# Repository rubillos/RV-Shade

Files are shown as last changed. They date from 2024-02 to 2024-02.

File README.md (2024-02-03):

# RV-Shade: HomeKit RV Shade controller

1. [Features](#features)
2. [Background](#background)
3. [Hardware](#hardware)
4. [Schematic](#schematic)
5. [Board Layout](#board-layout)
6. [Wiring](#wiring)
7. [Firmware Setup](#firmware)
8. [3D Printing](#3dprint)

## Features

* Arduino based circuit which intercepts the signals from the dash switch on an RV front shade to give HomeKit control.
* Built with an Adafruit QT Py ESP32-S3.
* Fits inside the front dash.
* STL files for a 3D printed case are included.

## Background

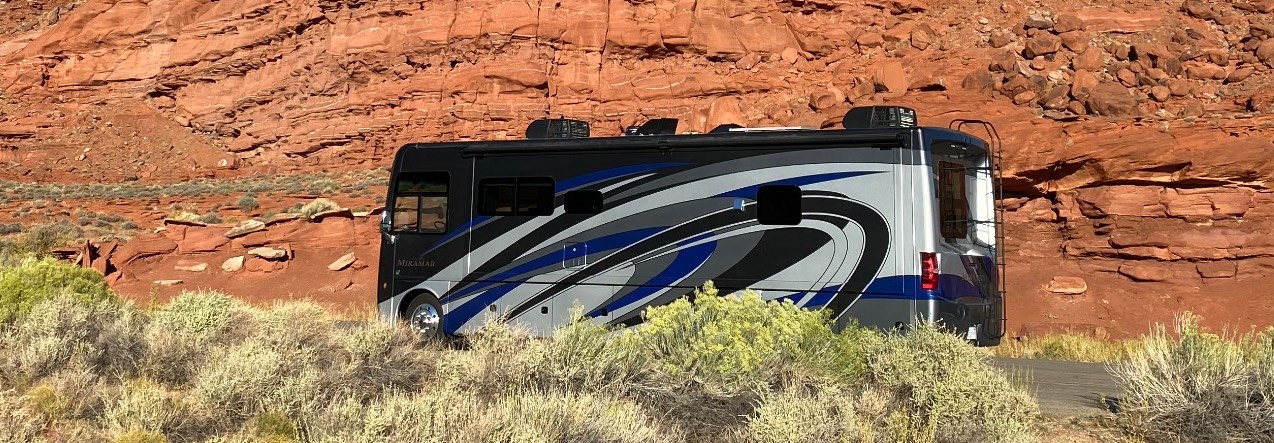
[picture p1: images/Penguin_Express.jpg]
Penguin Express


After purchasing a class-A motorhome in 2020 (***The Penguin Express***) I worked on several 3D and arduino projects for it. The first was a HomeKit to RV-C interface [RV-Bridge](https://github.com/rubillos/RV-Bridge). Since then I've done a couple of LED lighting controllers.

This project adds another controller to handle opening and closing the front shade via HomeKit.

## Hardware

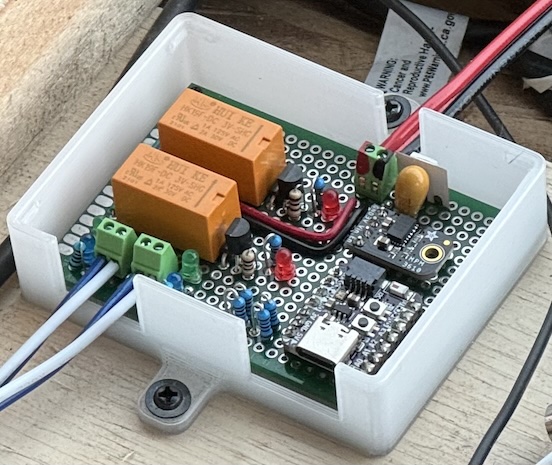
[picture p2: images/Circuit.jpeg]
Finished Circuit


The circuit is just an [Adafruit QT Py ESP32-S3 No PSRAM](https://www.adafruit.com/product/5426) with two 3V DPDT relays. One relay isolates the shade motor from the switch, the second drives the motor in either direction. There are some NPN MosFETs with flyback diodes for driving the relays and a pair of voltage dividers connected to analog inputs to read user actions on the switch. Some LEDs are wired to the switch and motor connectors as visual indicators.

Note: my QT Py had a non-functional NeoPixel so I hardwired an external one in it's place. You shouldn't need that, adjust the ifdef in the code accordingly.

## Schematic

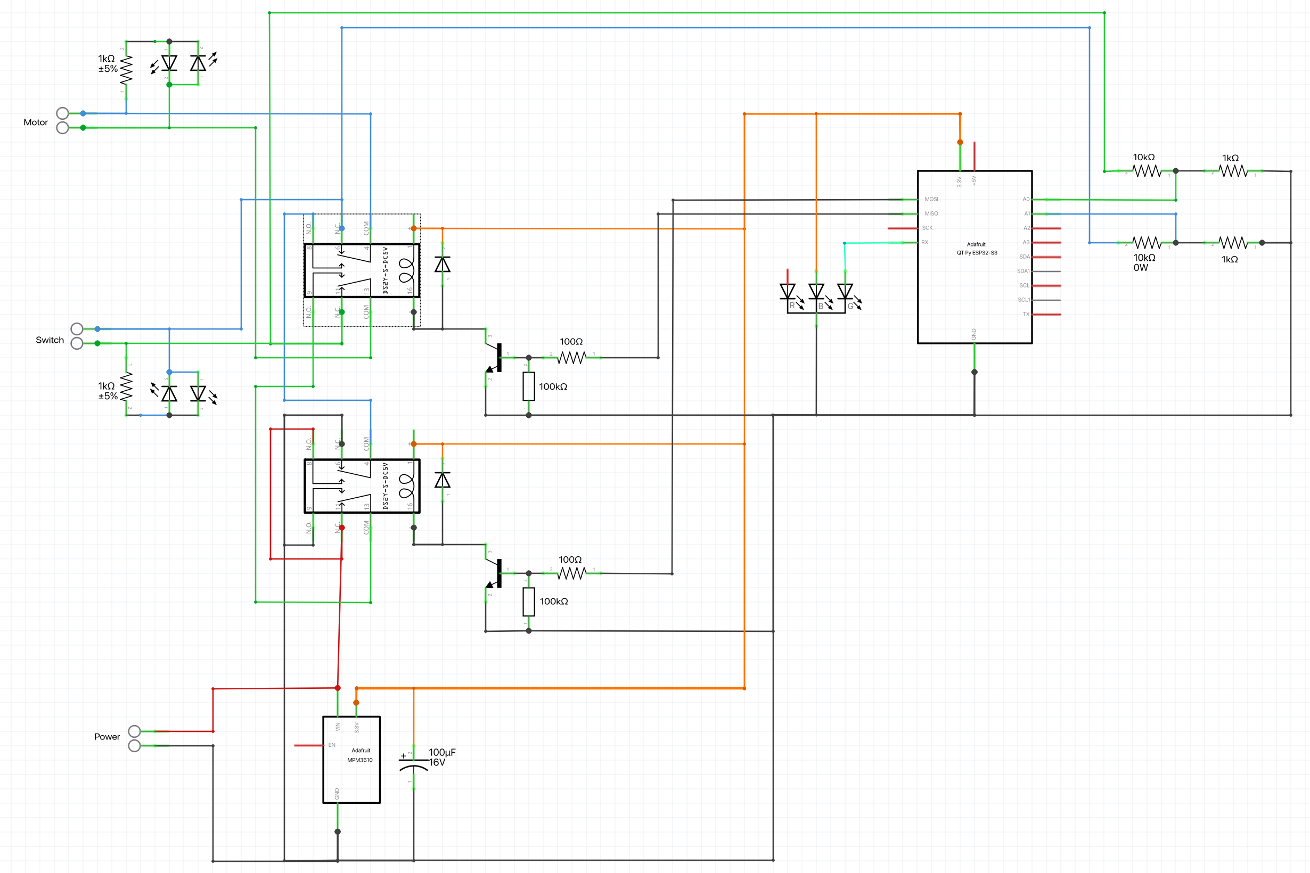
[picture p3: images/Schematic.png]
Schematic


## Board Layout

I use Fritzing for arranging board layout. I find that it's really good for figuring out where to place components for breadboard wiring.

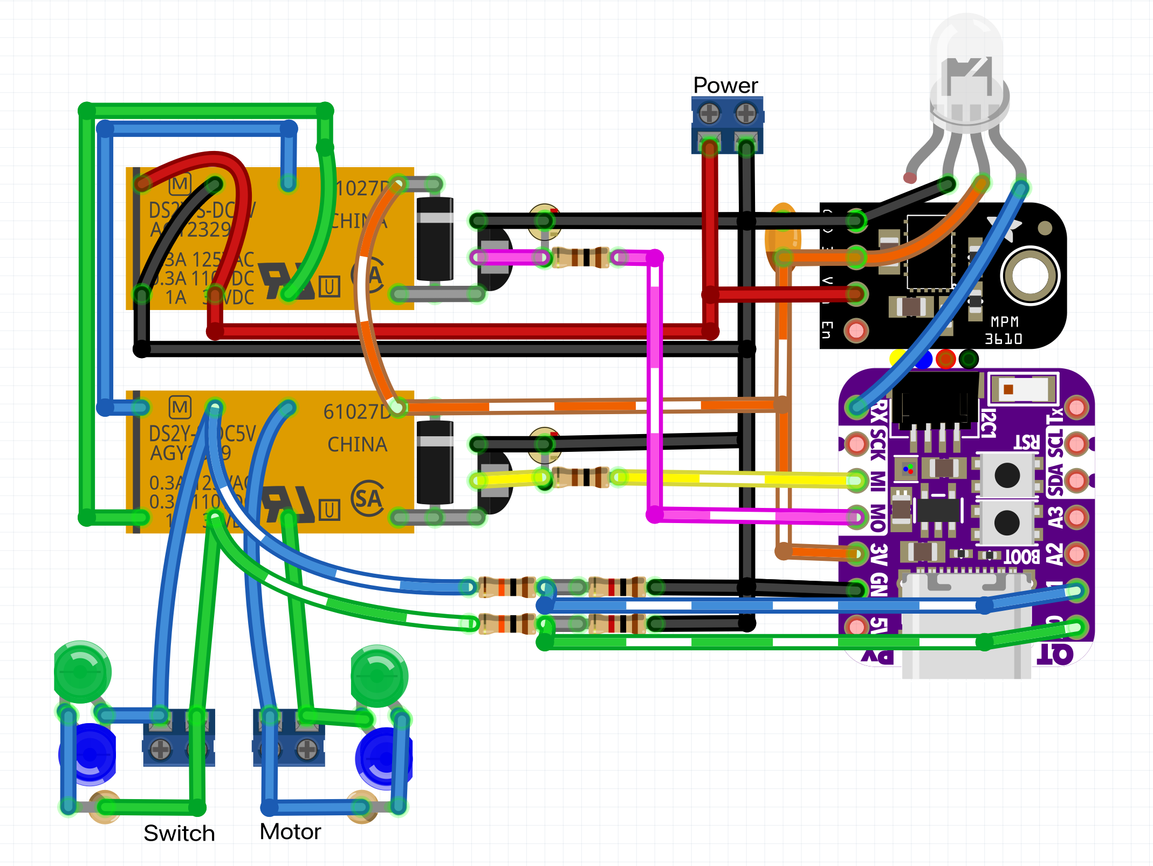
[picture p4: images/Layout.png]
Layout


## Wiring

The front shade on our RV is made by Irvine Shade. It has two control wires that connect to a switch on the dash. The switch is normally in the middle, you press and hold the top half to put the shade up, the bottom half moves the shade down.

After locating the two wires leading from the dash switch to the motor I cut them and used some [Inline Wire Splice Connectors](https://www.amazon.com/gp/product/B0BS6HZ941) to extend them up to the top of the dash, keeping track of which pair went to the switch and which went to the motor. I made sure to color code the extensions to the two wires.

I screwed the 3D printed enclosure to an empty spot under the dash cover, then spliced into 12V power that's active when the "house" power is on. (Make sure you don't tap into "chassis" power; I did that initially and spent some time figuring out why I wasn't seeing power).

|  |  |
| :---: | :---: |
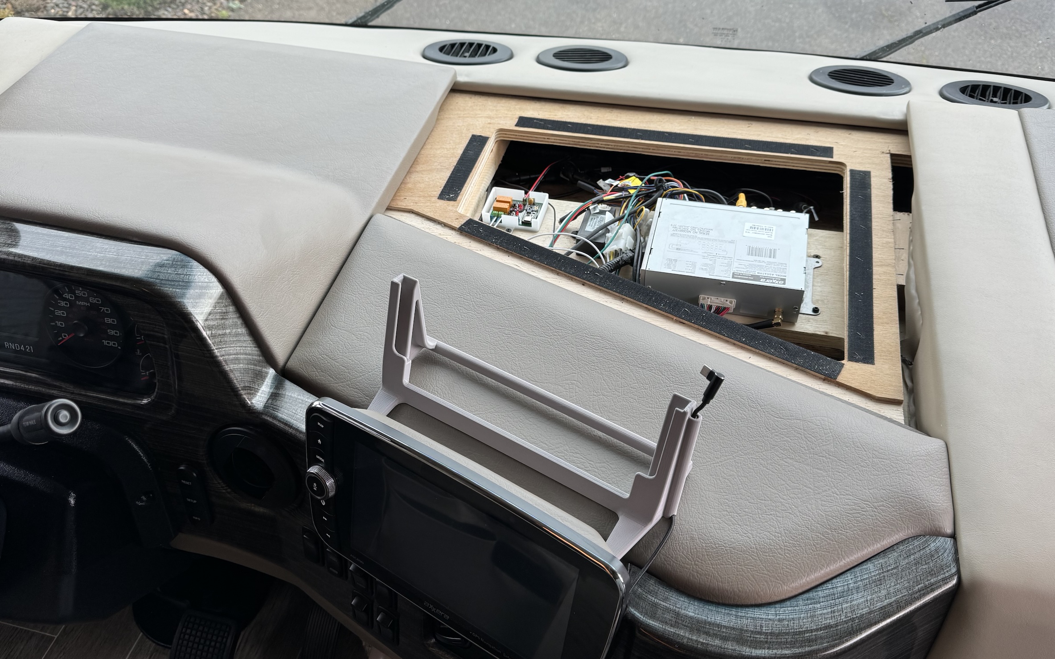
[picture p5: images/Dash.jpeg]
Dash
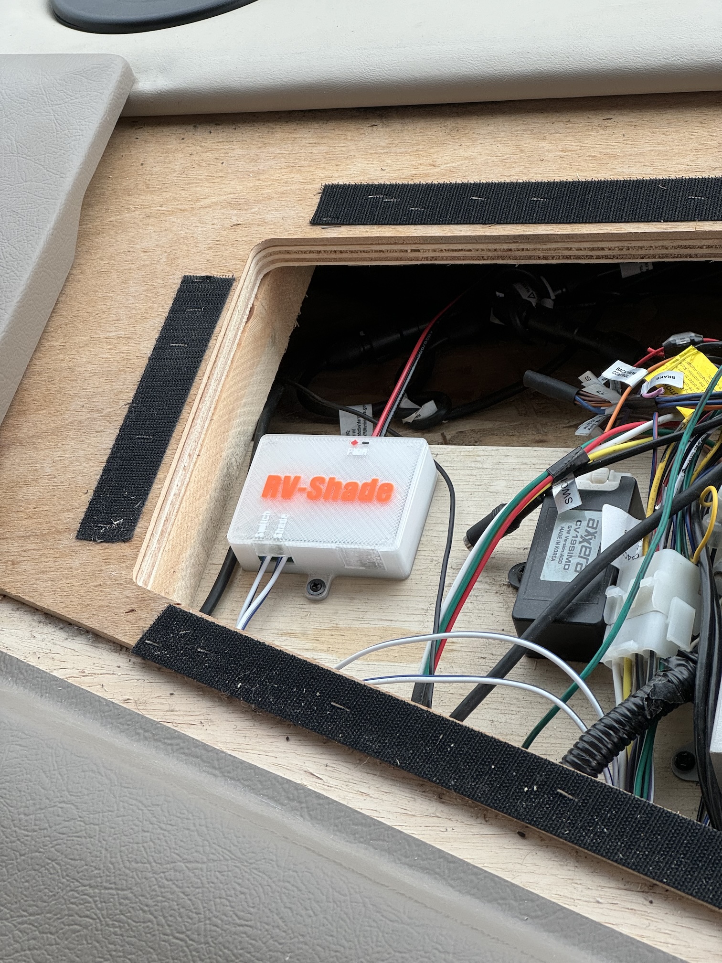
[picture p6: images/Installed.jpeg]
Installed
| <br> | |

## Firmware Setup

- The project is set up for compilation with PlatformIO.
    * I use it via Microsoft's Visual Studio Code.
- Flashing
    * The QT Py ESP32-S3 does not auto-reset after flashing, you need to do it manually.
- Startup
    * Connect to the ESP32 via the Serial Monitor.
    * You should see a bunch of startup logging.
    * Then a message about being connected to Wifi and not being paired.
    * HomeSpan provides a command line interface that you can access through the Serial Monitor. Type '?' to see the available comands.
- Pairing
    * Be on the same wifi network and in close proximity to the ESP32.
    * In the Home app choose "Add Accessory".
    * Point the camera at this image:
    <br><br>
    Pairing Code
    <br><br>
    * Tap on `RV-Shade`.
    * Accept that this is an "unsupported" device.
    * Add the bridge and the shade.
    * Done!

## 3D Printing

- A case will keep the microcontroller isolated from any exposed contacts inside the dash.
- STL Files are in the `3D` folder:
    * [RV-Shade_Box_Bottom.stl](/3D/RV-Shade_Box_Bottom.stl)
    * [RV-Shade_Box_Top.stl](/3D/RV-Shade_Box_Top.stl)
    * [Text](/3D/Text/) - There is a folder with STLs for each of the words. I have a Prusa XL and used these to have the text in different colors. You ca skip these and just have recessed words.
- Build Plate
    * A textured build plate give a nice surface finish for the top and bottom of the box.
- Filament
    * PETG - handles heat better than PLA and sticks to a textured build plate much better than PLA.

---
Copyright © 2024 [Randy Ubillos](http://rickandrandy.com)

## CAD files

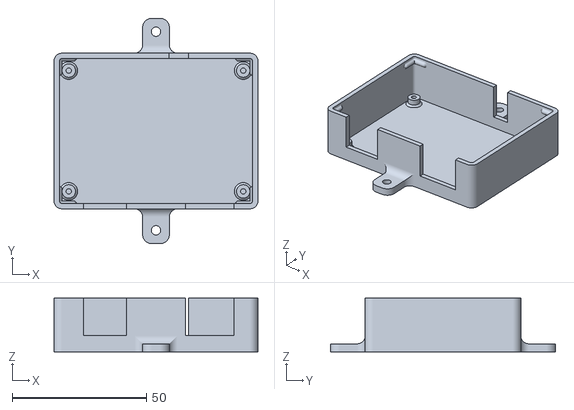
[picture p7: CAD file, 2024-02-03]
3D/RV-Shade_Box_Bottom.stl
76.0 x 84.0 x 20.0

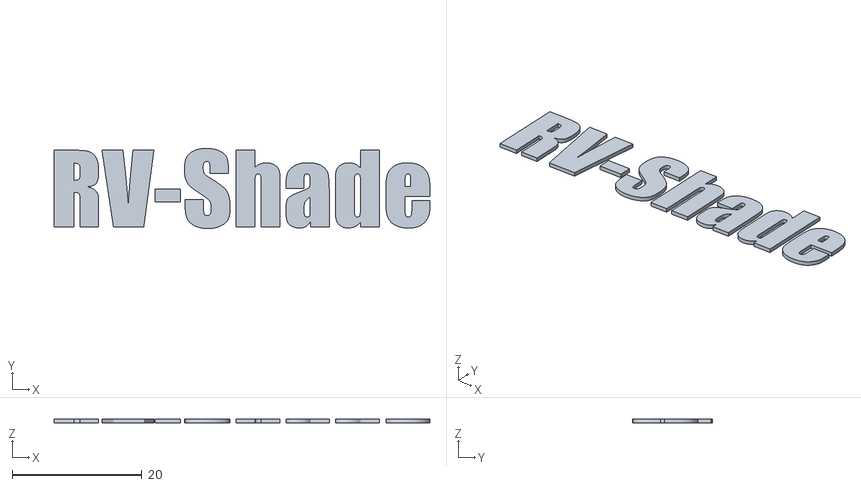
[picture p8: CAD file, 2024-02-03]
3D/Text/RV-Shade_Box_RV-Shade.stl
58.0 x 12.4 x 0.6

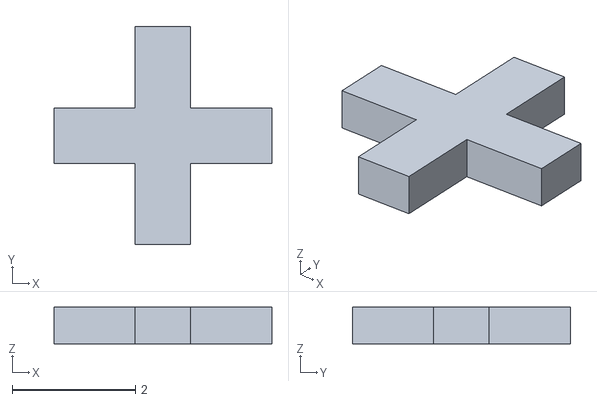
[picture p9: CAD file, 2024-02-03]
3D/Text/RV-Shade_Box_plus.stl
3.54 x 3.53 x 0.6

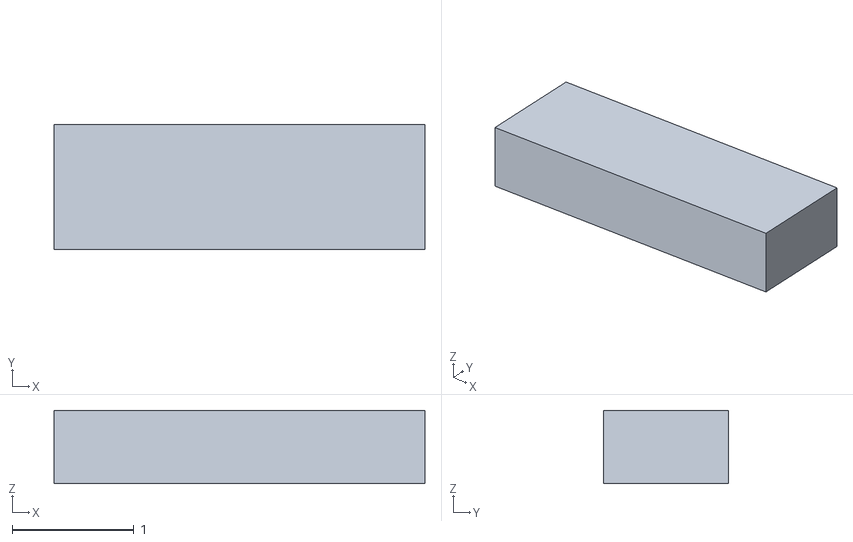
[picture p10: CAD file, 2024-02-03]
3D/Text/RV-Shade_Box_minus.stl
3.05 x 1.02 x 0.6

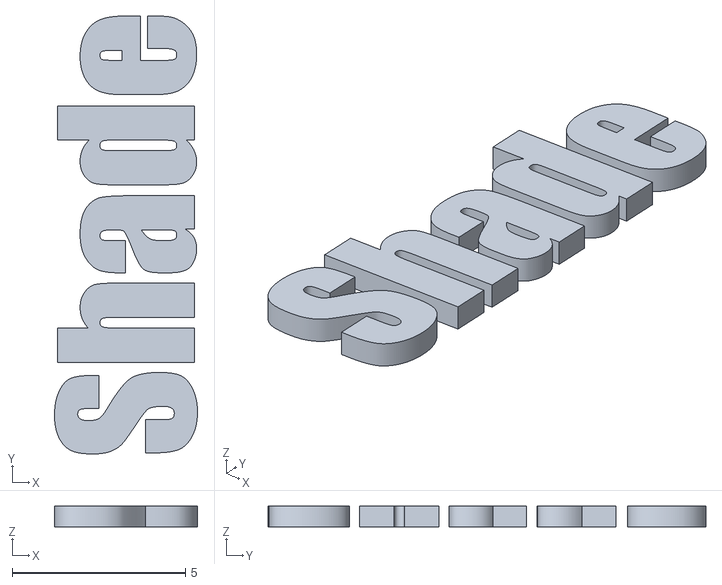
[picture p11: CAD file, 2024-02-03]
3D/Text/RV-Shade_Box_Shade.stl
4.12 x 12.6 x 0.6

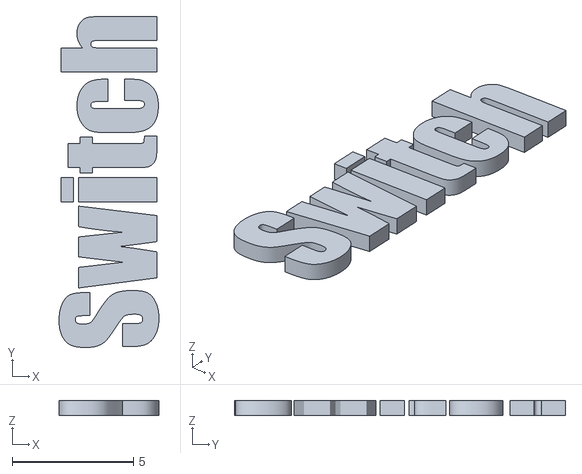
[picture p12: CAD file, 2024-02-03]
3D/Text/RV-Shade_Box_Switch.stl
4.12 x 13.7 x 0.6

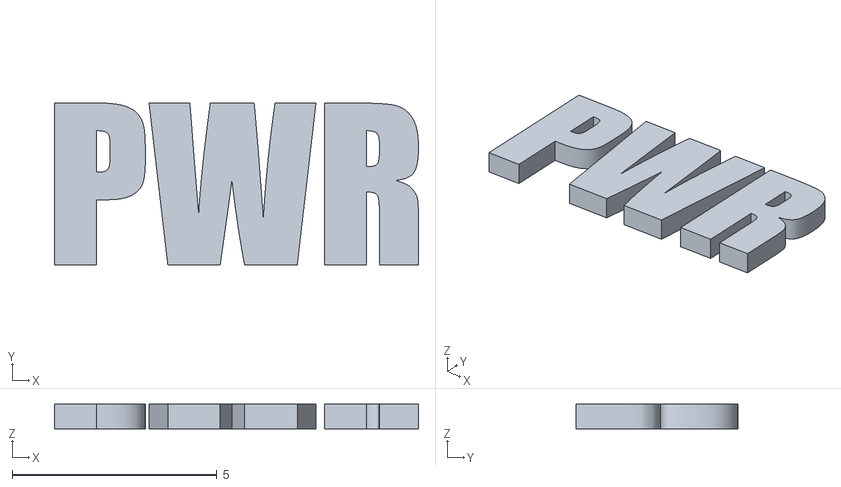
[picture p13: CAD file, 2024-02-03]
3D/Text/RV-Shade_Box_PWR.stl
8.89 x 3.96 x 0.6

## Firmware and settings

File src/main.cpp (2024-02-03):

#include <Arduino.h>

#include "HomeSpan.h" 
#include "Wire.h"
#include <Adafruit_NeoPixel.h>

#include <WiFi.h>
#include "driver/rmt.h"
#include "esp_log.h"

//////////////////////////////////////////////

constexpr const char* versionString = "v0.1";

constexpr const char* accessoryName = "Front Shade";

constexpr const char* displayName = "RV-Shade-Controller";
constexpr const char* modelName = "Shade-Controller-ESP32";

#if 0
constexpr int16_t indicatorDataPin = PIN_NEOPIXEL;
constexpr int16_t indicatorPowerPin = NEOPIXEL_POWER;
#else
constexpr int16_t indicatorDataPin = RX;
constexpr int16_t indicatorPowerPin = -1;
#endif

constexpr uint8_t controlOutputPin = MISO;
constexpr uint8_t directionOutputPin = MOSI;

constexpr uint32_t relaySettlingTimeMS = 8;

constexpr uint8_t openSensePin = A0;
constexpr uint8_t closeSensePin = A1;

constexpr uint16_t analogInputThreshold = 100;

constexpr uint32_t debounceTimeMS = 10;

//////////////////////////////////////////////

constexpr float homeKitFullScale = 100.0;

constexpr float homeKitShadeOpenValue = 100.0;
constexpr float homeKitShadeClosedValue = 0.0;

constexpr int homekitPositionStateClosing = 0;
constexpr int homekitPositionStateOpening = 1;
constexpr int homekitPositionStateStopped = 2;

//////////////////////////////////////////////

constexpr uint32_t indicatorTimeoutMS = 30 * 1000;

constexpr uint32_t closeTimeMS = 13 * 1000;
constexpr uint32_t openTimeMS = 15 * 1000;

constexpr uint32_t endStopExtraTimeMS = 500;

constexpr float closePerMS = homeKitFullScale / closeTimeMS;
constexpr float openPerMS = homeKitFullScale / openTimeMS;

constexpr uint32_t updateTimeMS = 500;

typedef uint16_t ShadeState;
constexpr uint16_t shadeStateClosing = 1 << 3;
constexpr uint16_t shadeStateOpening = 1 << 4;

constexpr uint16_t shadeStateUserAction = 1 < 5;
constexpr uint16_t shadeStateHomeKitAction = 1 << 6;

typedef uint16_t OutputState;
constexpr uint16_t outputStateIdle = 0;
constexpr uint16_t outputStateOpen = 1;
constexpr uint16_t outputStateClose = 2;

//////////////////////////////////////////////

bool wifiConnected = false;
bool hadWifiConnection = false;

#if defined(DEBUG)
// #define SerPrintf(...) Serial.printf(__VA_ARGS__)
#define SerPrintf(...) Serial.printf("%d: ", millis()); Serial.printf(__VA_ARGS__)
#define SerBegin(...) Serial.begin(__VA_ARGS__)
#else
#define SerPrintf(...)
#define SerBegin(...)
#endif

//////////////////////////////////////////////

uint64_t millis64() {
	volatile static uint32_t low32 = 0, high32 = 0;
	uint32_t new_low32 = millis();

	if (new_low32 < low32)
		high32++;

	low32 = new_low32;

	return (uint64_t) high32 << 32 | low32;
}

//////////////////////////////////////////////

constexpr uint8_t ledStatusLevel = 0x10;
constexpr uint32_t whiteColorFlag = 1 << 24;

#define MAKE_RGB(r, g, b) (r<<16 | g<<8 | b)
#define MAKE_RGB_STATUS(r, g, b) ((r*ledStatusLevel)<<16 | (g*ledStatusLevel)<<8 | (b*ledStatusLevel))
#define R_COMP(c) ((c>>16) & 0xFF)
#define G_COMP(c) ((c>>8) & 0xFF)
#define B_COMP(c) (c & 0xFF)

constexpr uint32_t blackColor = MAKE_RGB_STATUS(0, 0, 0);
constexpr uint32_t flashColor = MAKE_RGB_STATUS(1, 0, 1);
constexpr uint32_t startColor = MAKE_RGB_STATUS(0, 1, 1);
constexpr uint32_t connectingColor = MAKE_RGB_STATUS(0, 0, 1);

constexpr uint32_t openColor = MAKE_RGB(0, 1, 0);
constexpr uint32_t closedColor = MAKE_RGB(1, 0, 0);

uint32_t makeShadeColor(float level) {
	constexpr uint8_t ledBright = 30;
	constexpr uint8_t rL = ledBright * R_COMP(openColor);
	constexpr uint8_t gL = ledBright * G_COMP(openColor);
	constexpr uint8_t bL = ledBright * B_COMP(openColor);
	constexpr uint8_t rH = ledBright * R_COMP(closedColor);
	constexpr uint8_t gH = ledBright * G_COMP(closedColor);
	constexpr uint8_t bH = ledBright * B_COMP(closedColor);
	
	uint16_t r = rL + (rH - rL) * level;
	uint16_t g = gL + (gH - gL) * level;
	uint16_t b = bL + (bH - bL) * level;

	return MAKE_RGB(r, g, b);
}

//////////////////////////////////////////////

Adafruit_NeoPixel indicator(1, indicatorDataPin);
uint32_t currentIndicatorColor = 0xFFFFFFFF;

void setIndicator(uint32_t color) {
	if (color != currentIndicatorColor) {
		currentIndicatorColor = color;

		if (color & whiteColorFlag) {
			color &= 0xFF;
			indicator.setPixelColor(0, color, color, color);
		}
		else {
			indicator.setPixelColor(0, R_COMP(color), G_COMP(color), B_COMP(color));
		}
		indicator.show();
	}
}

void setIndicator8(uint8_t color8) {
	setIndicator(whiteColorFlag | color8);
}

void flashIndicator(uint32_t color, uint16_t count, uint16_t period) {
	for (auto i=0; i<count; i++) {
		setIndicator(color);
		delay(period/4);
		setIndicator(0);
		delay(period*3/4);
	}
}

void updateIndicator(ShadeState state, float shadePosition) {
	static uint64_t lastStoppedTime = 0;
	uint64_t curTime = millis64();
	uint32_t color;
	bool moving = (state & (shadeStateOpening | shadeStateClosing)) != 0;

	if ((lastStoppedTime == 0) || moving) {
		lastStoppedTime = curTime;
	}

	if (!wifiConnected && ((millis()%600) < 200)) {
		color = connectingColor;
	}
	else if (moving && ((millis()%200) < 30)) {
		color = blackColor;
	}
	else if (curTime - lastStoppedTime >= indicatorTimeoutMS) {
		color = blackColor;
	}
	else {
		color = makeShadeColor(shadePosition / homeKitFullScale);
	}

	setIndicator(color);
}

//////////////////////////////////////////////

class ButtonBase {
	public:
		ButtonBase(uint8_t pin) : _pin(pin) {}
		virtual bool isPressed();
		bool pressed() {
			bool result = false;
			bool currentPress = isPressed();

			if (currentPress) {
				uint64_t curTime = millis64();
				if (_pressed) {
					result = (curTime-_pressTime) > debounceTimeMS;
				}
				else {
					_pressed = true;
					_pressTime = curTime;
				}
			}
			else {
				_pressed = false;
			}
			return result;
		}

	protected:
		uint8_t _pin;
		bool _pressed = false;
		uint64_t _pressTime;
};

class ButtonDigital : public ButtonBase {
	public:
		ButtonDigital(uint8_t pin) : ButtonBase(pin) {
			pinMode(_pin, INPUT_PULLUP);
		};
		bool isPressed() { return digitalRead(_pin)==LOW; };
};

class ButtonAnalog : public ButtonBase {
	public:
		ButtonAnalog(uint8_t pin) : ButtonBase(pin) {};
		bool isPressed() { return analogRead(_pin) > analogInputThreshold; };
};

//////////////////////////////////////////////

class OutputPin {
	public:
		OutputPin(uint8_t pin) : _pin(pin) {
			setPin(LOW);
			pinMode(_pin, OUTPUT);
		}

		void setState(uint8_t state, uint32_t delay = 0) {
			if (delay) {
				_delayedState = state;
				_delayedStateTime = millis64() + delay;
			}
			else {
				setPin(state);
			}
		}

		void clearDelayedState() {
			_delayedState = -1;
		}

		void update(uint64_t curTime) {
			if (_delayedState != -1 && curTime > _delayedStateTime) {
				setPin(_delayedState);
				clearDelayedState();
			}
		}

		uint8_t state() { return _state; }

	private:
		uint8_t _pin = 0;
		int16_t _state = -1;
		int16_t _delayedState = -1;
		uint64_t _delayedStateTime = 0;

		void setPin(uint8_t state) {
			if (state != _state) {
				digitalWrite(_pin, state);
				_state = state;
			}
		}
};

struct RVShade : Service::WindowCovering {
	SpanCharacteristic* _currentPosition = NULL;
	SpanCharacteristic* _targetPosition = NULL;
	SpanCharacteristic* _positionState = NULL;

	ButtonAnalog* _userOpenButton = NULL;
	ButtonAnalog* _userCloseButton = NULL;

	OutputPin* _controlPin = NULL;
	OutputPin* _directionPin = NULL;

	ShadeState _shadeState = 0;
	float _currentShadePosition = homeKitShadeOpenValue;
	uint64_t _nextPositionUpdateTime = 0;

	OutputState _outputState = outputStateIdle;

	uint64_t _operationEndTime;

	RVShade() : Service::WindowCovering() {
		_currentPosition = new Characteristic::CurrentPosition(homeKitShadeOpenValue);
		_targetPosition = new Characteristic::TargetPosition(homeKitShadeOpenValue);
		_positionState = new Characteristic::PositionState(homekitPositionStateStopped);

		_userOpenButton = new ButtonAnalog(openSensePin);
		_userCloseButton = new ButtonAnalog(closeSensePin);

		_controlPin = new OutputPin(controlOutputPin);
		_directionPin = new OutputPin(directionOutputPin);
	}

	boolean update() {
		if (_targetPosition->updated()) {
			uint64_t curTime = millis64();

			float targetValue = _targetPosition->getNewVal<float>();
			float moveAmount = targetValue - _currentShadePosition;
			uint32_t moveTimeMS = abs(moveAmount / homeKitFullScale) * ((moveAmount > 0) ? openTimeMS : closeTimeMS);

			_operationEndTime = curTime + moveTimeMS;

			if (targetValue == homeKitShadeClosedValue || targetValue == homeKitShadeOpenValue) {
				_operationEndTime += endStopExtraTimeMS;
			}

			_shadeState = shadeStateHomeKitAction | ((moveAmount > 0) ? shadeStateOpening : shadeStateClosing);

			SerPrintf("Changing position from %0.1f%% to %0.1f%% over %dmS.\n", _currentShadePosition, targetValue, (int)(_operationEndTime-curTime));
			SerPrintf("State changed to 0x%02X\n", _shadeState);
		}
		return true;
	}

	void loop() {
		static uint64_t lastTime = 0;
		uint64_t curTime = millis64();

		if (lastTime == 0) {
			lastTime = curTime;
		}

		if (curTime > lastTime) {
			bool needPositionUpdate = false;
			bool needTargetUpdate = false;

			if (_userOpenButton->pressed()) {
				_shadeState = shadeStateUserAction | shadeStateOpening;
			}
			else if (_userCloseButton->pressed()) {
				_shadeState = shadeStateUserAction | shadeStateClosing;
			}
			else if (_shadeState & shadeStateUserAction) {
				_shadeState = 0;
				needTargetUpdate = true;
			}

			bool moving = (_shadeState & (shadeStateOpening | shadeStateClosing)) != 0;
			bool movingOpen = (_shadeState & shadeStateOpening) != 0;

			if (moving) {
				_currentShadePosition += (curTime - lastTime) * ((movingOpen) ? openPerMS : -closePerMS);
				_currentShadePosition = max(homeKitShadeClosedValue, min(homeKitShadeOpenValue, _currentShadePosition));

				if (_shadeState & shadeStateHomeKitAction && curTime > _operationEndTime) {
					_currentShadePosition = _targetPosition->getVal<float>();
					_shadeState = 0;
					SerPrintf("Homekit operation complete.\n");
				}
			}

			OutputState newOutputState;

			if (_shadeState & shadeStateHomeKitAction) {
				newOutputState = (_shadeState & shadeStateOpening) ? outputStateOpen : outputStateClose;
			}
			else {
				newOutputState = outputStateIdle;
			}

			if (newOutputState != _outputState) {
				SerPrintf("Output state changed to %d\n", newOutputState);

				_controlPin->clearDelayedState();
				_directionPin->clearDelayedState();

				bool newDirectionOutputState;
				bool newControlOutputState;

				if (newOutputState == outputStateOpen) {
					newDirectionOutputState = LOW;
					newControlOutputState = HIGH;
				}
				else if (newOutputState == outputStateClose) {
					newDirectionOutputState = HIGH;
					newControlOutputState = HIGH;
				}
				else {
					newDirectionOutputState = LOW;
					newControlOutputState = LOW;
				}

				if (newDirectionOutputState != _directionPin->state() && newControlOutputState != _controlPin->state()) {
					if (newControlOutputState == HIGH) {		// direction  needs time to settle before setting control
						_controlPin->setState(newControlOutputState, relaySettlingTimeMS);
						_directionPin->setState(newDirectionOutputState, 0);
					}
					else {									// direction needs to hold while control settles
						_controlPin->setState(newControlOutputState, 0);
						_directionPin->setState(newDirectionOutputState, relaySettlingTimeMS);
					}
				}
				else {
					_controlPin->setState(newControlOutputState, 0);
					_directionPin->setState(newDirectionOutputState, 0);
				}

				_outputState = newOutputState;
				needPositionUpdate = true;
			}

			if (needPositionUpdate || needTargetUpdate || (_nextPositionUpdateTime>0 && curTime > _nextPositionUpdateTime)) {
				if (needTargetUpdate || _shadeState & shadeStateUserAction) {
					float nextPosition = _currentShadePosition;
					
					if (_shadeState & shadeStateOpening) {
						 nextPosition = min(homeKitShadeOpenValue, _currentShadePosition + openPerMS * updateTimeMS);
					}
					else if (_shadeState & shadeStateClosing) {
						 nextPosition = max(homeKitShadeClosedValue, _currentShadePosition - closePerMS * updateTimeMS);
					}

					if (_targetPosition->getVal<float>() != nextPosition) {
						_targetPosition->setVal(nextPosition);
						SerPrintf("Target changed to %0.1f%%\n", nextPosition);
					}
				}
				if (_currentPosition->getVal<float>() != _currentShadePosition) {
					_currentPosition->setVal(_currentShadePosition);
					SerPrintf("Position changed to %0.1f%% - output=%d\n", _currentShadePosition, _outputState);
				}
				_nextPositionUpdateTime = 0;
			}

			if (moving && _nextPositionUpdateTime == 0) {
				_nextPositionUpdateTime = curTime + updateTimeMS;
			}

			_controlPin->update(curTime);
			_directionPin->update(curTime);

			updateIndicator(_shadeState, _currentShadePosition);

			int movingState = (moving) ? ((movingOpen ? homekitPositionStateOpening : homekitPositionStateClosing)) : homekitPositionStateStopped;
			if (movingState != _positionState->getVal()) {
				_positionState->setVal(movingState);
			}

			lastTime = curTime;
		}
	}
};

//////////////////////////////////////////////

RVShade* shade;

void createDevices() {
	SPAN_ACCESSORY();   // create Bridge

	SPAN_ACCESSORY(accessoryName);
		shade = new RVShade();
}

//////////////////////////////////////////////

void statusChanged(HS_STATUS status) {
	if (status == HS_WIFI_CONNECTING) {
		wifiConnected = false;
		if (hadWifiConnection) {
			SerPrintf("Lost WIFI Connection...\n");
		}
	}
}

void wifiReady() {
	wifiConnected = true;
	hadWifiConnection = true;
	SerPrintf("WIFI: Ready.\n");
}

//////////////////////////////////////////////

void setup() {
	if (indicatorPowerPin != -1) {
		pinMode(indicatorPowerPin, OUTPUT);
		digitalWrite(indicatorPowerPin, HIGH);
	}
	
	indicator.begin();

	#ifdef DEBUG
	flashIndicator(flashColor, 20, 200);
	setIndicator(startColor);
	#endif

	SerBegin(115200);
	SerPrintf("RV-Shade Startup\n");

	SerPrintf("Init HomeSpan...\n");
	homeSpan.setSketchVersion(versionString);
	homeSpan.setWifiCallback(wifiReady);
	homeSpan.setStatusCallback(statusChanged);
	homeSpan.enableWebLog(50);
	homeSpan.begin(Category::Bridges, displayName, DEFAULT_HOST_NAME, modelName);

	SerPrintf("Create devices...\n");
	createDevices();

	SerPrintf("Init complete.\n");

	SerPrintf("Wait for WiFi...\n");
	setIndicator(connectingColor);
}

void loop() {
	homeSpan.poll();

	// HomeSpan does not call the wifi callback after the first connection
	// We do that manually here
	if (hadWifiConnection && !wifiConnected) {
		static uint64_t nextWifiCheck = 0;
		uint64_t time = millis64();

		if (time >= nextWifiCheck) {
			if (WiFi.status()==WL_CONNECTED) {
				wifiReady();
			}

			nextWifiCheck = time + 500;
		}
	}
}
